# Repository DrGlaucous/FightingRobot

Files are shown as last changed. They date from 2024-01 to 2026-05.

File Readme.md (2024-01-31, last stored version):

# Remote Vehicle repository

This is where I put everything relating to designing a small, "antweight" combat robot.

## Firmware
Currently, the firmware is programmed in platform.io around the STM32 architecture.
The vehicle communicates to the controller using the RFM69HW radio module, which is both inexpensive and has excellent transmission range.

The "Transmitter" module decodes [PPM signals](http://flyingeinstein.com/index.php/articles/58-ppm-explained) from the controller and sends their digital values over the radio to the vehicle. There *are* recievers that output PPM directly without the need for the RFM middleman, but those are expensive and radio-specific. The extra range those modules would provide would be moot in the context of miniature combat robots. The analog transmitters additionally do not provide the customization abillity the digital transmiter has.

The work with RFM69 radios builds upon my previous project where I made an [inexpensive iClicker alternative using just the radio and an STM32](https://github.com/DrGlaucous/LittleBuddy). That repository better outlines how the STM32 should be connected to the RFM69 module.

---

<details>
  <summary style="font-size:100%;"><i><b>Notes for me</b></i></summary>

### Future Goals
Either use an ESP32 on the vehicle-side, or add bidirectional DShot to the STM32, so the vehicle's motor will provide telemetry.

### Mobility
With the transmitter, more flexible motion can be implemented.

Current suggestion: 3 wheeled omniwheel wheelbase

### Weapons

Rotating offset platic blade on one side, must not be below or above the robot's dirve train so it can drive upside down or rightside up.

Or long, plastic wedge attached to a servo motor for flipping other robots.

</details>

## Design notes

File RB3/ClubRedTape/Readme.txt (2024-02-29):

Things required by the club this robot is entered into in order to get it certified and usable.

these CAD files must also be on arris
part naming conventsions:

[4-letter-code]-[A/P - assembly/part]-[2 digit asm ID][2 digit part ID]Name
example:
OMNI-P-0203SideStrut

ASM Ids:
00 - top
1 - asm sketch
2 - chassis
3 - drivebase
4 - weapon1
5 - weapon2
6 - ground game (wedges/forks)

(also, it all has to be in solidworks, for some reason...)

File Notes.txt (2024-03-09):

hardware SPI on an ESP32:
default:

VSPI:
MOSI 23
MISO 19
SCLK 18
CS 5

HSPI
MOSI 13
MISO 12
SCLK 14
CS 15

in arduino IDE, these are defined as their respective names
(note: these pins can be changed)

to change SPI pins manually in a library that doesn't support custom initialization, use:
SPI.begin(SCK, MISO, MOSI, SS);

for multiple SPI busses, initialize
vspi = new SPIClass(VSPI);
hspi = new SPIClass(HSPI);

see more:
https://randomnerdtutorials.com/esp32-spi-communication-arduino/

on top and bottom walls, other robots use 1.5-2mm thick shells

(we could probably do this for the internal structure as well)

for edge walls, 3-5mm will suffice (put curves so the robot cannot sit on them)

Futaba 12 channel troubles:

reset line is

long time LOW->long time HIGH

each channel has a LOW time that matches a HIGH time

A channel may unexpectedly cut out before transmission is complete, completing a "cycle" prematurely.
it will wait at least one complete cycle before finishing the half-done channel.

in order to ensure that we get good signals every time, we need to detect the bad channel pauses.
The easiest way to (possibly) do this is to only update all the channel values if we get all of them in one go.

if we detect a reset rollover, we then move the waiting signals over to the visible surface ONLY if we got all of them. Partials will not count.

have roughly 7 Oz on frame

1.295 allocated for screws, worst case

5.705 left for frame
(some screws can be ommitted/glue used instead)

16 Oz max

1.0005 - PCB + componets
3.327 - wheels + n20s * 3
1.01 - 2205
0.30 - ESC
0.976 - servos
2 - battery
1.295 - screws

-9.88 for all of this

2.196 - side walls

6 Ounces/170 grams to work with

Blade: 9g
Internal frame (as-is) + arm: 84

(thin top shell, both sides: 60g)

12.08 total rn + side walls

oz
3.73 - walls+roof
0.81 - mot1
2.6320 - mot2
2.238 - wheels3
2.74 - chassis + electrics
2.00 - battery
14.292 - total

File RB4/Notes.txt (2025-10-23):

BOM items:

x2 4mm motors

optional amazon things:
openWRT router
large bullet connectors
4mm bearings

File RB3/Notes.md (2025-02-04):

### BOM

- 1 lolin32 lite
- 1 littlebee ESC
- 1 2205 brushless motor
- 1 motor driver
- x2 n30 motors + encoders
- 3d prints

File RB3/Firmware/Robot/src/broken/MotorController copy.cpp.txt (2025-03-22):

#include <Arduino.h>
#include <math.h>
#include "configuration.h"
#include "PidController.h"
#include "MotorController.h"

static void isr_0();
static Apple* this_0;

static void isr_1();
static Apple* this_1;

void isr_0() {
    this_0->isr_handler();
}
void isr_1() {
    this_1->isr_handler();
}

void Apple::isr_handler() {

    bool CLKstate = digitalRead(enca_pin);
    bool DTstate = digitalRead(encb_pin);

    switch (encoder_state) {
        case 0:                         // Idle state, encoder not turning
            if (!CLKstate){             // Turn clockwise and CLK goes low first
                encoder_state = 1;
            } else if (!DTstate) {      // Turn anticlockwise and DT goes low first
                encoder_state = 4;
            }
            break;
        // Clockwise rotation
        case 1:                     
            if (!DTstate) {             // Continue clockwise and DT will go low after CLK
                encoder_state = 2;
            } 
            break;
        case 2:
            if (CLKstate) {             // Turn further and CLK will go high first
                encoder_state = 3;
            }
            break;
        case 3:
            if (CLKstate && DTstate) {  // Both CLK and DT now high as the encoder completes one step clockwise
                encoder_state = 0;
                ++encoder_value;
            }
            break;
        // Anticlockwise rotation
        case 4:                         // As for clockwise but with CLK and DT reversed
            if (!CLKstate) {
                encoder_state = 5;
            }
            break;
        case 5:
            if (DTstate) {
                encoder_state = 6;
            }
            break;
        case 6:
            if (CLKstate && DTstate) {
                encoder_state = 0;
                --encoder_value;
            }
            break; 
    }

}

/*
MotorController::MotorController(
    int enca_pin,
    int encb_pin,
    int motor_a_pin,
    int motor_b_pin,
    IsrSlotNumber slot_num
    ) {
    
    this->enca_pin = enca_pin;
    this->encb_pin = encb_pin;
    this->motor_a_pin = motor_a_pin;
    this->motor_b_pin = motor_b_pin;

    this->has_began = false;
    
    this->slot_num = slot_num;

    motor_pid = PIDControllerF_construct(
        ANALOG_MIN,
        ANALOG_MAX,
        -ANALOG_MAX,
        0.2, //p
        0.2, //i
        0.2 //d
    );

    //set proper ISR
    switch(slot_num) {
        case IsrSlotZero: {
            this_0 = this;
            attachInterrupt(enca_pin, isr_0, CHANGE);
            attachInterrupt(encb_pin, isr_0, CHANGE);
            break;
        }
        case IsrSlotOne: {
            this_1 = this;
            attachInterrupt(enca_pin, isr_0, CHANGE);
            attachInterrupt(encb_pin, isr_0, CHANGE);
            break;
        }
    }

}
*/

Apple::Apple() {

}

Apple::~Apple() {
    PIDControllerF_destruct(motor_pid);

    detachInterrupt(enca_pin);
    detachInterrupt(encb_pin);

    // switch(slot_num) {
    //     case IsrSlotZero: {
    //         this_0 = this;
    //         detachInterrupt(enca_pin);
    //         detachInterrupt(encb_pin);
    //         break;
    //     }
    //     case IsrSlotOne: {
    //         this_1 = this;
    //         attachInterrupt(enca_pin, isr_0, CHANGE);
    //         attachInterrupt(encb_pin, isr_0, CHANGE);
    //         break;
    //     }
    // }
}

void Apple::begin() {
    //set up IO
    pinMode(motor_a_pin, OUTPUT);
    pinMode(motor_b_pin, OUTPUT);
    pinMode(enca_pin, INPUT);
    pinMode(encb_pin, INPUT);

    analogWrite(motor_a_pin, ANALOG_MIN);
    analogWrite(motor_b_pin, ANALOG_MIN);

    has_began = true;

}

float Apple::tick(int target_speed, bool is_disabled, bool direct_speed_map) {

    //inputs
    //int target_speed = 0; //raw controller speed (from NORMAL_MIN to NORMAL_MAX)
    //bool is_disabled = false; //true when the main robot disables the motor controller

    //true when the input speed should be mapped directly to the motors
    //can be used if the PID breaks or something
    //bool direct_speed_map = false;

    //must have initialized and be enabled
    if(!has_began || is_disabled) {
        return 0.0;
    }

    //note: this may not be used, depending on stability (with my nerf blaster, using a non-constant for this resulted in trouble)
    int milliss = millis();

    //do not run if no time has elapsed
    // if(milliss == last_millist) {
    //     return 0.0;
    // }

    //turn raw controller input into a target RPM speed for the motor
    //note: 200 ticks per rotation

    //get current RPM (may be less than one per tick)
    float curr_rpm = 0.0;
    {
        int delta_ticks = motor_tick_ct - last_motor_tick_ct;
        float tick_fraction = 0.0;

        if(delta_ticks) {
            time_since_motor_tick = 0;
            tick_fraction = delta_ticks;
        } else {
            time_since_motor_tick++;
            tick_fraction = 1.0 / ((float)time_since_motor_tick);
        }

        //tick_fraction is the number of ticks we have since the last time checked

        float minutes_elapsed = ((float)(milliss - 0) * 0.001 * 0.016666);
        float rpm = tick_fraction / minutes_elapsed;

        curr_rpm = tick_fraction;
        last_motor_tick_ct = motor_tick_ct;
    }

    if(direct_speed_map) {
        motor_output = map(target_speed, NORMAL_MIN, NORMAL_MAX, -ANALOG_MAX, ANALOG_MAX);
    } else {

        int mapped_target_speed = rpm_to_ticks(map(target_speed, NORMAL_MIN, NORMAL_MAX, -100, 100));
        PIDControllerF_tick(motor_pid, FLOAT_TO_FIXED32(curr_rpm), INT_TO_FIXED32(mapped_target_speed), 200); //feeding constant time step of 200 into the PID
    }

    //last_millist = milliss;

    return curr_rpm;

}

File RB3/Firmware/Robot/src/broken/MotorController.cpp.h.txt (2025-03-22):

#pragma once

#define ANALOG_MAX 255
#define ANALOG_MIN 0

typedef enum IsrSlotNumber {
    IsrSlotZero,
    IsrSlotOne
}IsrSlotNumber;

class MotorController{

    public:

    MotorController(
        int enca_pin,
        int encb_pin,
        int motor_a_pin,
        int motor_b_pin,
        IsrSlotNumber sl
    );

    ~MotorController();

    void begin();

    float tick(int target_speed, bool is_disabled, bool direct_speed_map);

    void isr_handler();

    private:

    int enca_pin = -1;
    int encb_pin = -1;
    int motor_a_pin = -1;
    int motor_b_pin = -1;

    int motor_output = 0; //value to be written to the motor (result of the PID or direct mapping)
    bool has_began = false;

    int last_millis = 0;
    int motor_tick_ct = 0; //holds raw absolute position of the motor
    int last_motor_tick_ct = 0; //for delta ticks
    int time_since_motor_tick = 0; //holds the number of cycles since the last encoder change interrupt

    // uint8_t encoder_state = 0;

    // PIDControllerF* motor_pid = NULL;
    // IsrSlotNumber slot_num = IsrSlotOne; //keep track of this for removing ISR on destruct
    // int32_t encoder_value = 0;

    // // //isrs (one for each instance of the class we can run)
    // // static void isr_0();
    // // static MotorController* this_0;

    // // static void isr_1();
    // // static MotorController* this_1;

};

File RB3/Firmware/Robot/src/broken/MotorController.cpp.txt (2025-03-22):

#include "Apple.h"

int rpm_to_ticks(int rpm) {
    return rpm * 200;
}

void MotorController::isr_handler() {

}

MotorController::MotorController(
    int enca_pin,
    int encb_pin,
    int motor_a_pin,
    int motor_b_pin,
    IsrSlotNumber sl
    ) {

}

MotorController::~MotorController() {

}

void MotorController::begin() {

}

float MotorController::tick(int target_speed, bool is_disabled, bool direct_speed_map) {
    return 0.0;
}

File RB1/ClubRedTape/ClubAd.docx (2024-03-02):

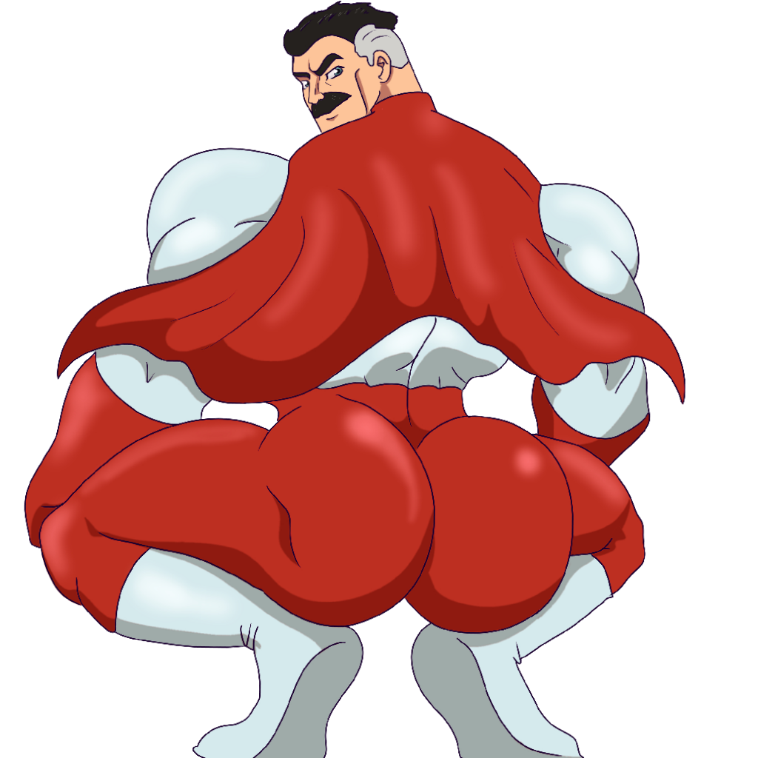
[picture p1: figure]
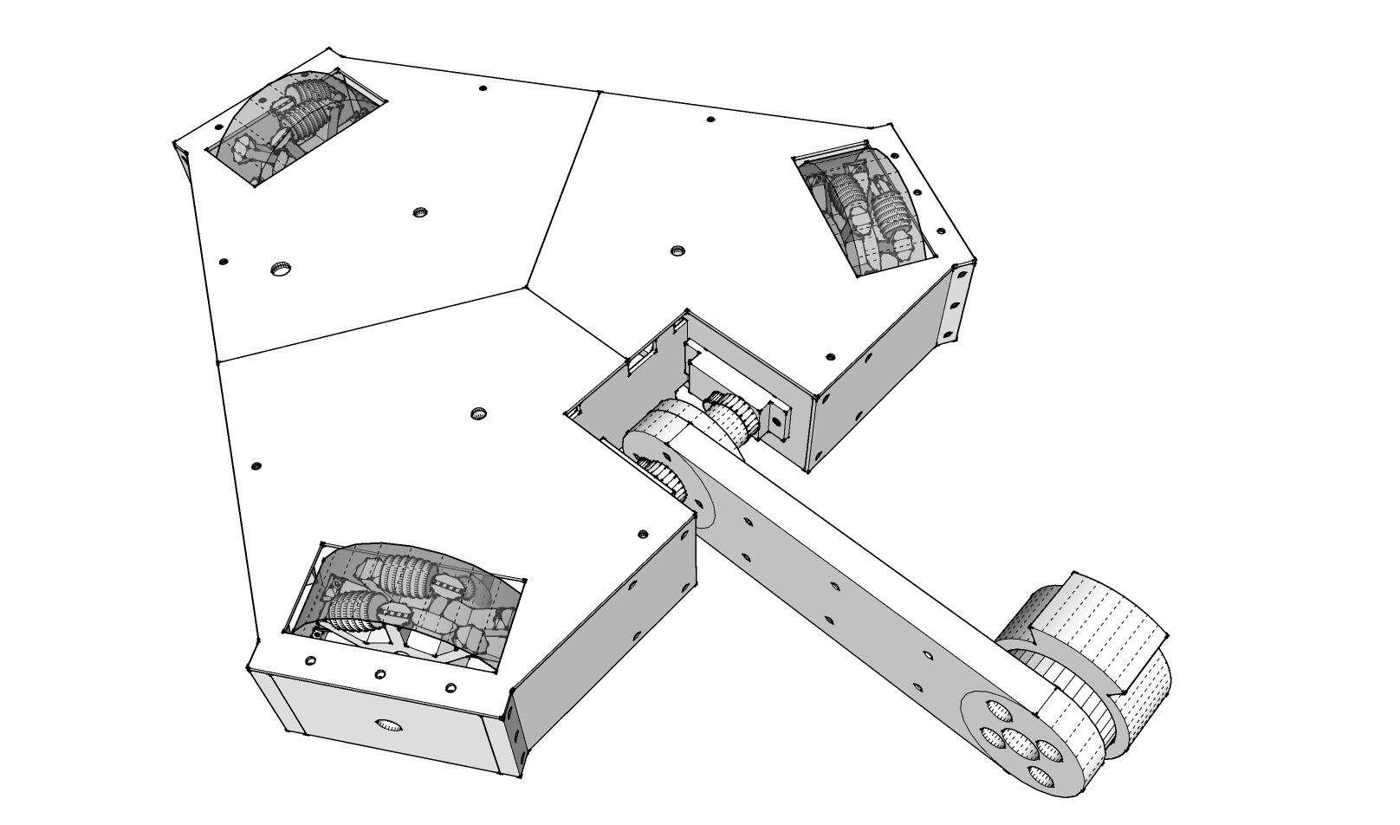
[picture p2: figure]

See this robot dump its truck on others like it on 3/23/2024 at 10:00 AM in Aspire Building A. The event is free to watch!

At the 2024 Railside Robotics

Battlebot Brawl!

Root for Omni-Man!

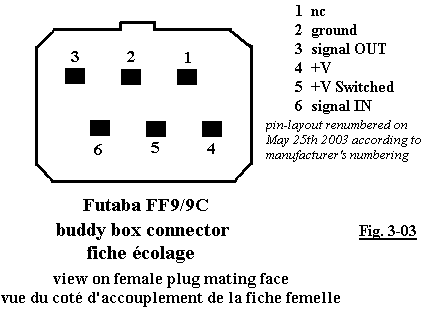
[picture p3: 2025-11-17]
Resource/Futaba trainer port pinout.gif

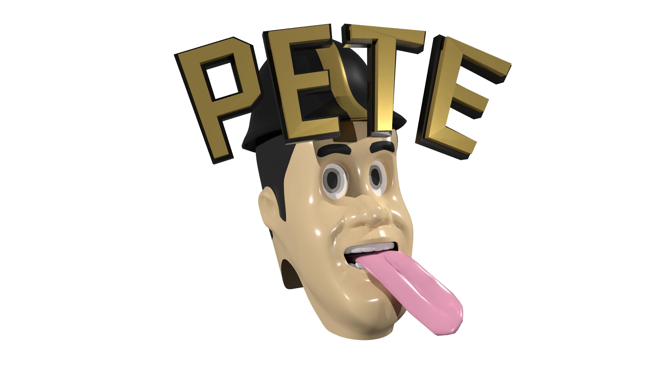
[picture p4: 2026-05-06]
RB4/Media/Pete.png

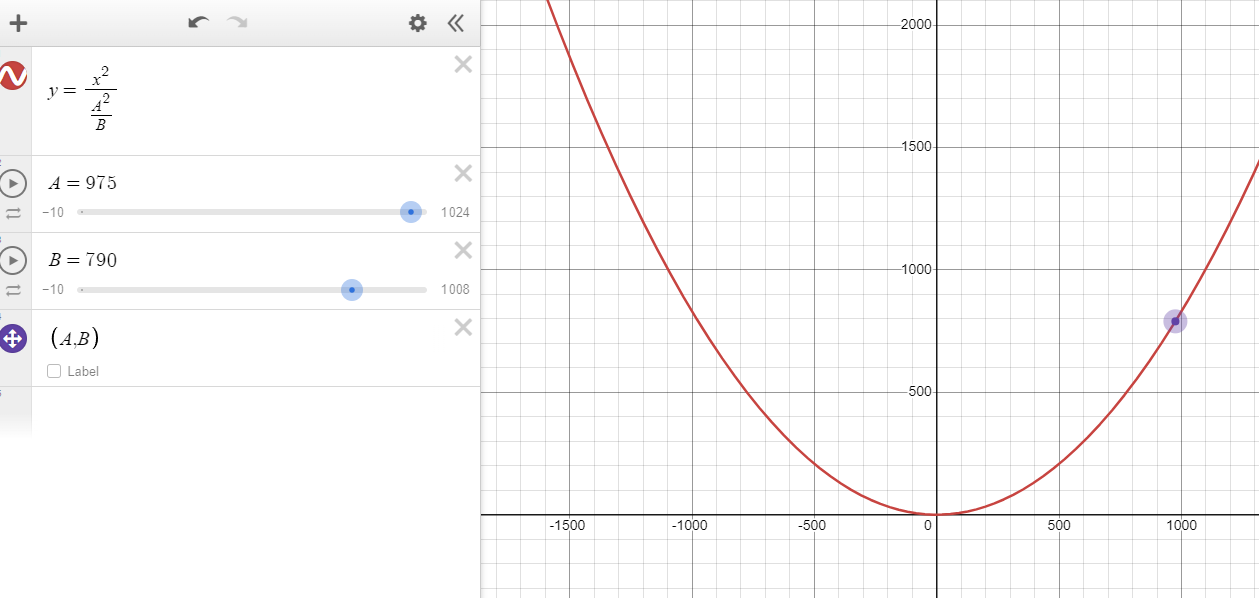
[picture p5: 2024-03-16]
RB1/Resource/ExponentialMapping.PNG

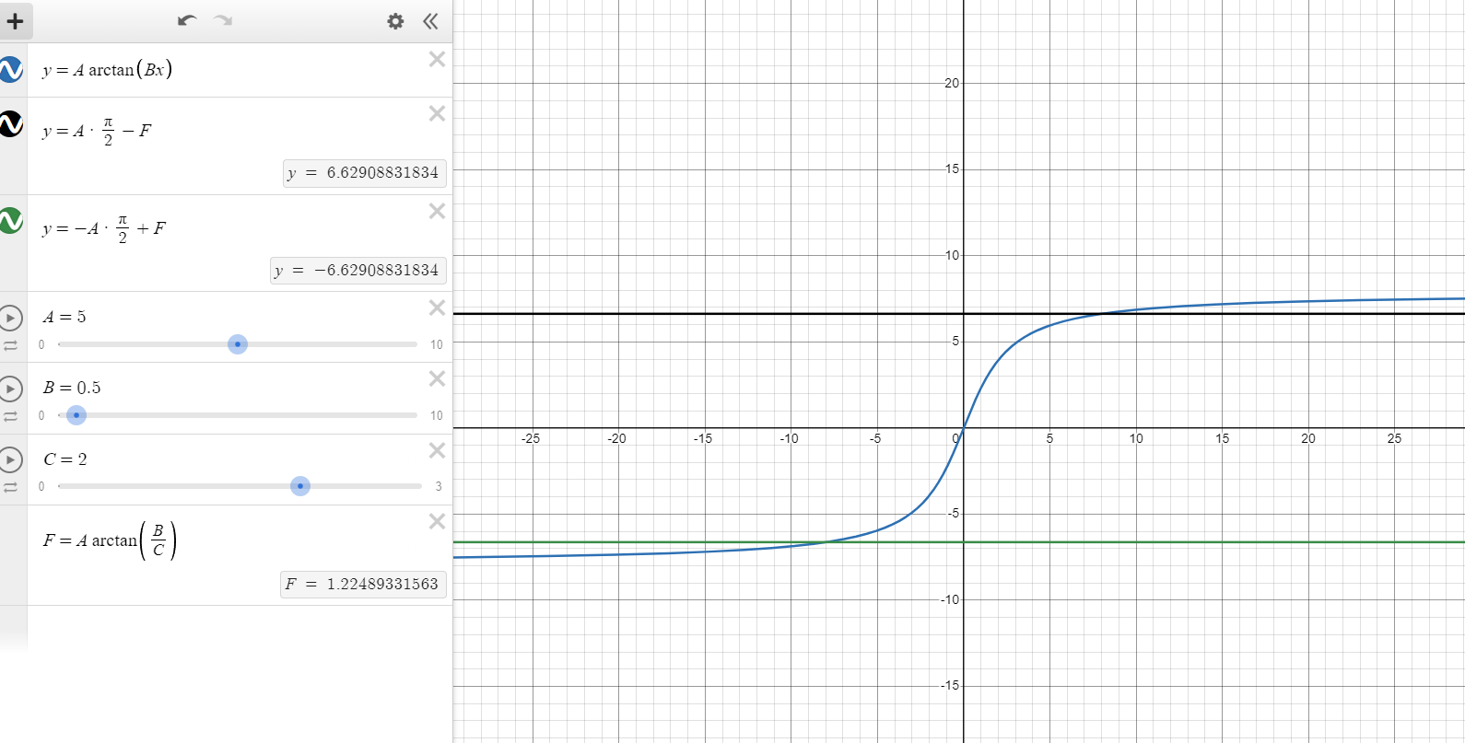
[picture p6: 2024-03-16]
RB1/Resource/MotorSpeedRampFunction.PNG

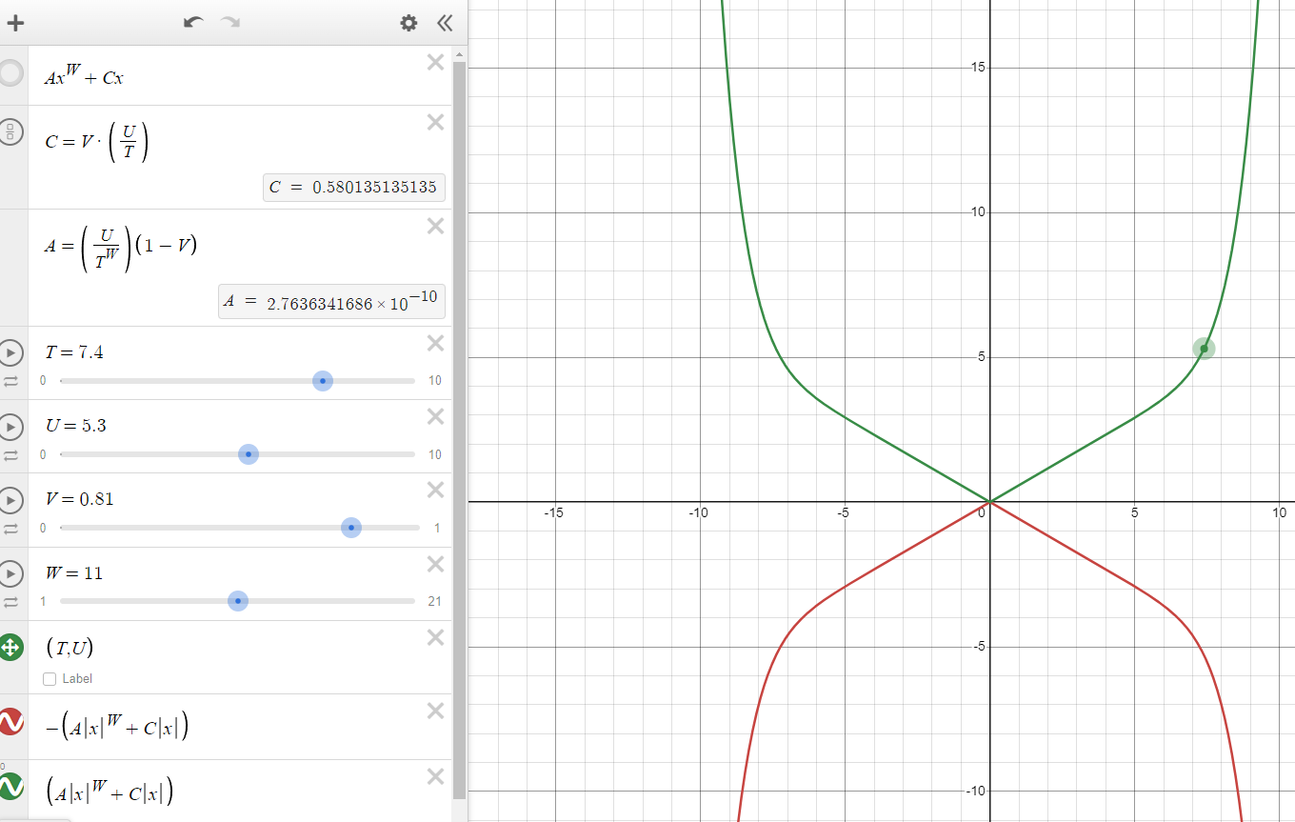
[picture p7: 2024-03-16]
RB1/Resource/RotattionRampEquation.PNG

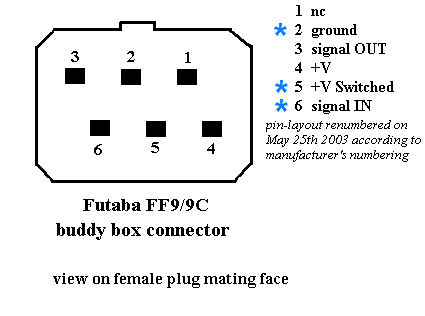
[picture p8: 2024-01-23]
RB1/Resource/futabaplug.jpg

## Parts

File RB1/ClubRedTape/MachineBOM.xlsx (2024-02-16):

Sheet: BOM
DO NOT ENTER VALUES FOR COLUMNS HIGHLIGHTED GREEN
Overall Bot Value: |  | $84.35 | External Component $ Spent: | $202.96 | Railside $ Spent: | $30.74 | Total $ Spent: | $233.70
Category | Qty | Item | Specs | Item Description | Vendor/Source | Link | Units per Package | Units per Bot | Provided by Railside? | Item Cost | What is the part for? | Unit Cost | Unit/Bot Cost | Total Cost
 | 1 | Fingertech Mini Power Switch | N.A. | Screw switch used to turn robot on / off | Itgresa | https://itgresa.com/product/mini-power-switch/ | 1 | 1 | yes | $7.99 | Required Safety | $7.99 | $7.99 | $7.99
 | 1 | Tattu 450 mAh 2S LiPo with XT30 | 75C 450mAh | Battery to power the robot | Amazon | https://www.amazon.com/TATTU-450mAh-Battery-Pack-H-Frame/dp/B07DTYN9QF?s=electronics | 1 | 1 | yes | $12.95 | Power | $12.95 | $12.95 | $12.95
 | 1 | N20 gearmotor | 12 Volt, 1000 RPM | For Robot Drive Base | AliExpress | https://www.aliexpress.com/item/2251832836005412.html | 1 | 3 | no | $1.68 | Mobility | $1.68 | $5.04 | $1.68
 | 1 | N20 gearmotor (alt. source) | 12 Volt, 800 RPM | Alt. Club provided Drive Base motors | itgresa | https://itgresa.com/product/turnabot-n20-motors-1400rpm/ | 1 | 3 | yes | $9.80 | Mobility (backup) | $9.80 | $29.40 | $9.80
 | 1 | RFM69HW Radio Tranciever | 915Mhz, 1.4kbps | For remote interfacing | AliExpress | https://www.aliexpress.com/item/3256803259645975.html | 1 | 2 | no | $1.66 | Remote Control | $1.66 | $3.32 | $1.66
Electronics | 1 | LittleBee ESC | BLHELI_S, 30A | For driving the weapon | Amazon | https://www.amazon.com/LITTLEBEE-Mulitshot-Oneshot42-OneShot125-Multicopter/dp/B09P44FKKQ | 4 | 1 | no | $30.00 | Weapon Driver | $7.50 | $7.50 | $30.00
 | 1 | 2205 Emax Motor | 2300KV, 2205 | Used as the weapon | Amazon | https://www.amazon.com/AKK-RS2205-Brushless-2300KV-Quadcopter/dp/B07BQRGT7Q | 4 | 1 | no | $31.99 | Weapon | $8.00 | $8.00 | $31.99
 | 1 | Fuse | 15A max | Overcurrent safety | Unknown |  | 2 | 2 | yes | $0.00 | Required Safety | $0.00 | $0.00 | $0.00
 | 1 | DRV8833 DC motor driver | handles 2 motors | For Robot Drive Base | AliExpress | https://www.aliexpress.com/item/3256806258295019.html | 10 | 2 | no | $4.64 | Mobility | $0.46 | $0.93 | $4.64
 | 1 | XL60009 Boost module | 4A in max, 12 volts out | Motor power supply | Amazon | https://www.amazon.com/AITRIP-Voltage-Adjustable-Step-up-Converter/dp/B08FM414QN | 10 | 1 | no | $14.00 | Power Regulation | $1.40 | $1.40 | $14.00
 | 1 | Mini360 Buck module | 3.3 volt out | Logic power supply | AliExpress | https://www.aliexpress.us/item/3256806205076602.html | 20 | 1 | no | $2.00 | Power Regulation | $0.10 | $0.10 | $2.00
 | 1 | Lolin32 LITE | 32 bit microcontroller | Bot controller | AliExpress | https://www.aliexpress.com/item/3256801612417572.html | 1 | 1 | no | $2.12 | Bot Control | $2.12 | $2.12 | $2.12
 | 1 | STM32 Bluepill | 32 bit microcontroller | Transmitter controller | AliExpress | https://www.aliexpress.us/item/3256806245533637.html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 | 10 | 1 | no | $14.00 | Remote Control | $1.40 | $1.40 | $14.00
 | 1 | MG90S Servo | All-metal MG90S | micro servo | AliExpress | https://www.aliexpress.com/item/3256805876746809.html | 10 | 2 | no | $16.37 | Weapon | $1.64 | $3.27 | $16.37
 |  | Things like power transmission members (belts, pulleys), bot materials (3D printer filament), wheels, bushings/bearings, etc go here |  |  |  |  |  |  |  | $0.00 |  | $0.00 | $0.00 | $0.00
 | 1 | ABS (Home-Extruded) | PA757 | Natural uncolored ABS | Filastruder |  | 50 | 0.5 | no | $80.00 | Frame | $1.60 | $0.80 | $80.00
Structure / Materials | 1 |  |  |  |  |  |  |  |  | $0.00 |  | $0.00 | $0.00 | $0.00
 | 1 |  |  |  |  |  |  |  |  | $0.00 |  | $0.00 | $0.00 | $0.00
 | 1 |  |  |  |  |  |  |  |  | $0.00 |  | $0.00 | $0.00 | $0.00
 |  | Screws, nuts, shoulder bolts go here |  |  |  |  |  |  |  | $0.00 |  | $0.00 | $0.00 | $0.00
 | 1 | 6-32x1-1/2 Phillips screw | 6-32x1-1/2 | Machine screw | Menards | In-store | 100 | 3 | no | $2.25 | Fasteners | $0.02 | $0.07 | $2.25
Hardware (Fasteners) | 1 | 6-32 Hex Nut | 6-32 size | Machine nut | Menards | In-Store | 100 | 3 | no | $2.25 | Fasteners | $0.02 | $0.07 | $2.25
 | 1 | Plastic Screw | #4 | self-tapping screw | Amazon | https://www.amazon.com/Thread-Rolling-Plastic-Finish-Degree/dp/B00GDYNQBM | 100 | 50 | yes | $0.00 | Fasteners | $0.00 | $0.00 | $0.00
 |  |  |  |  |  |  |  |  |  | $0.00 |  | $0.00 | $0.00 | $0.00
 |  | Anything that doesnt fit into the above category |  |  |  |  |  |  |  | $0.00 |  | $0.00 | $0.00 | $0.00
 |  |  |  |  |  |  |  |  |  | $0.00 |  | $0.00 | $0.00 | $0.00
Misc. |  |  |  |  |  |  |  |  |  | $0.00 |  | $0.00 | $0.00 | $0.00
 |  |  |  |  |  |  |  |  |  | $0.00 |  | $0.00 | $0.00 | $0.00
 |  |  |  |  |  |  |  |  |  | $0.00 |  | $0.00 | $0.00 | $0.00
 |  |  |  |  |  |  |  |  |  | $0.00 |  | $0.00 | $0.00 | $0.00
 |  |  |  |  |  |  |  |  |  | $0.00 |  | $0.00 | $0.00 | $0.00
 |  |  |  |  |  |  |  |  |  | $0.00 |  | $0.00 | $0.00 | $0.00
 |  |  |  |  |  |  |  |  |  | $0.00 |  | $0.00 | $0.00 | $0.00
 |  |  |  |  |  |  |  |  |  | $0.00 |  | $0.00 | $0.00 | $0.00
 |  |  |  |  |  |  |  |  |  | $0.00 |  | $0.00 | $0.00 | $0.00
 |  |  |  |  |  |  |  |  |  | $0.00 |  | $0.00 | $0.00 | $0.00
 |  |  |  |  |  |  |  |  |  | $0.00 |  | $0.00 | $0.00 | $0.00
 |  |  |  |  |  |  |  |  |  | $0.00 |  | $0.00 | $0.00 | $0.00
 |  |  |  |  |  |  |  |  |  | $0.00 |  | $0.00 | $0.00 | $0.00
 |  |  |  |  |  |  |  |  |  | $0.00 |  | $0.00 | $0.00 | $0.00
 |  |  |  |  |  |  |  |  |  | $0.00 |  | $0.00 | $0.00 | $0.00
 |  |  |  |  |  |  |  |  |  | $0.00 |  | $0.00 | $0.00 | $0.00

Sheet: Equations
Input yellow values | Green values will automatically be calculated
Battery
Cells | Voltage Level | Voltage Multiplier | Voltage (V)
2 | max | 4.2 | 8.4
Weapon Motor
Kv (rpm/V) | Throttle % | RPM | Kv (rad/s/V)
0 | 100 | 0 | 0
Weapon
Moment of Inertia (g*mm^2) | Diameter (in) | Weapon Reduction
0 | 0 | 1
MOI (kg*m^2) | RPM | (rev/s) | Angular Velocity (rad/s)
0 | 0 | 0 | 0
Kinetic Energy (Joules) | Tip Speed (in/s) | Tip Speed (mph)
0 | 0 | 0
Bite
Impactor Count | Max Impactor Angle (fraction) | Seconds per Hit (s) | Max Bite (in)
0 | #DIV/0! | #DIV/0! | #DIV/0!
Drive Motor
RPM | Throttle % | RPM
0 | 100 | 0
Drive
Wheel Diameter (in) | Speed (in/min) | Speed (mph) | Speed (in/s)
0 | 0 | 0 | 0

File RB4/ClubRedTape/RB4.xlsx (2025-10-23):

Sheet: BOM
DO NOT ENTER VALUES FOR COLUMNS HIGHLIGHTED GREEN
Overall Bot Value: |  | $59.47 | External Component $ Spent: | $25.90 | Railside $ Spent | $4.99 | Total $ Spent: | $30.89
Category | Qty | Item | Ordering Specs | Vendor/Source | Link | Subsystem | Units per Package | Units per Bot | Provided by Railside? | Item Cost | What is the part for? | Unit Cost | Unit/Bot Cost | Total Cost
 | 1 | PCB power switch |  | JustCuz | https://justcuzrobotics.com/products/switch | Electronics | 1 | 1 | yes | $4.99 | Robot power | $4.99 | $4.99 | $4.99
 | 2 | 1200 mAh 2S LiPo with XT30 |  | Amazon | https://www.amazon.com/URGENEX-Battery-1200mAh-Rechargeable-Compatible/dp/B0DZNYQWD4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 (https://www.amazon.com/TATTU-450mAh-Battery-Pack-H-Frame/dp/B07DTYN9QF?s=electronics) | Electronics | 2 | 1 | no | $12.95 | Robot power | $6.47 | $6.47 | $25.90
 |  | Drive motors, mk.2 brushed, 4mm shaft |  | Repeat Robotics | https://repeat-robotics.com/buy/brushed/ | Drivetrain | 1 | 2 | no | $20.00 | robot drive | $20.00 | $40.00 | $0.00
 |  | ESP32 - C3 |  | aliExpress | N.A | Electronics | 1 | 1 | no | $2.00 | robot control | $2.00 | $2.00 | $0.00
Electronics |  | DRV8833 |  | aliExpress | N.A | Electronics | 1 | 1 | no | $1.00 | motor control | $1.00 | $1.00 | $0.00
 |  | MG996R servo |  | aliExpress | N.A | Weapon | 1 | 1 | no | $5.00 | weapon drive | $5.00 | $5.00 | $0.00
 |  | RFM69HW Radio |  | aliExpress | N.A | Electronics |  |  |  | $0.00 | communication | $0.00 | $0.00 | $0.00
 |  | Fuse |  | N.A. |  |  |  |  |  | $0.00 | Fuse not needed | $0.00 | $0.00 | $0.00
 |  |  |  |  |  |  |  |  |  | $0.00 |  | $0.00 | $0.00 | $0.00
 |  | TPU Filament |  |  |  | Chassis |  |  |  | $0.00 | Bot frame | $0.00 | $0.00 | $0.00
Structure / Materials |  |  |  |  |  |  |  |  |  | $0.00 |  | $0.00 | $0.00 | $0.00
 |  |  |  |  |  |  |  |  |  | $0.00 |  | $0.00 | $0.00 | $0.00
 |  | N.A.
Power Transmission |  |  |  |  |  |  |  |  |  | $0.00 |  | $0.00 | $0.00 | $0.00
 |  |  |  |  |  |  |  |  |  | $0.00 |  | $0.00 | $0.00 | $0.00
 |  | Screws, nuts, shoulder bolts go here |  |  |  |  |  |  |  | $0.00 |  | $0.00 | $0.00 | $0.00
 |  | Plastic screws, club supplied (1/2 inch) |  | X |  | Chassis | X | 15 | yes | $0.00 | Bot fasteners | $0.00 | $0.00 | $0.00
Hardware (Fasteners) |  | Plastic screws, club supplied (3/4 inch) |  | X |  | Chassis | X | 10 | yes | $0.00 | Bot fasteners | $0.00 | $0.00 | $0.00
 |  |  |  |  |  |  |  |  |  | $0.00 |  | $0.00 | $0.00 | $0.00
 |  |  |  |  |  |  |  |  |  | $0.00 |  | $0.00 | $0.00 | $0.00
 |  | Anything that doesnt fit into the above category |  |  |  |  |  |  |  | $0.00 |  | $0.00 | $0.00 | $0.00
 |  |  |  |  |  |  |  |  |  | $0.00 |  | $0.00 | $0.00 | $0.00
Misc. |  |  |  |  |  |  |  |  |  | $0.00 |  | $0.00 | $0.00 | $0.00
 |  |  |  |  |  |  |  |  |  | $0.00 |  | $0.00 | $0.00 | $0.00
 |  |  |  |  |  |  |  |  |  | $0.00 |  | $0.00 | $0.00 | $0.00
 |  |  |  |  |  |  |  |  |  | $0.00 |  | $0.00 | $0.00 | $0.00
 |  |  |  |  |  |  |  |  |  | $0.00 |  | $0.00 | $0.00 | $0.00
 |  |  |  |  |  |  |  |  |  | $0.00 |  | $0.00 | $0.00 | $0.00
 |  |  |  |  |  |  |  |  |  | $0.00 |  | $0.00 | $0.00 | $0.00
 |  |  |  |  |  |  |  |  |  | $0.00 |  | $0.00 | $0.00 | $0.00
 |  |  |  |  |  |  |  |  |  | $0.00 |  | $0.00 | $0.00 | $0.00
 |  |  |  |  |  |  |  |  |  | $0.00 |  | $0.00 | $0.00 | $0.00
 |  |  |  |  |  |  |  |  |  | $0.00 |  | $0.00 | $0.00 | $0.00
 |  |  |  |  |  |  |  |  |  | $0.00 |  | $0.00 | $0.00 | $0.00
 |  |  |  |  |  |  |  |  |  | $0.00 |  | $0.00 | $0.00 | $0.00
 |  |  |  |  |  |  |  |  |  | $0.00 |  | $0.00 | $0.00 | $0.00
 |  |  |  |  |  |  |  |  |  | $0.00 |  | $0.00 | $0.00 | $0.00
 |  |  |  |  |  |  |  |  |  | $0.00 |  | $0.00 | $0.00 | $0.00

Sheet: Physics Equations
Input yellow values | Green values will automatically be calculated
Battery
Cells | Voltage Level | Voltage Multiplier | Voltage (V)
3 | nominal | 3.7 | 11.1
Weapon Motor
Kv (rpm/V) | Throttle % | RPM | Kv (rad/s/V)
1800 | 100 | 19980 | 188.4955592
Weapon
Moment of Inertia (g*mm^2) | Diameter (in) | Weapon Reduction
244900 | 4 | 1
MOI (kg*m^2) | RPM | (rev/s) | Angular Velocity (rad/s)
0.0002449 | 19980 | 333 | 2092.300707
Kinetic Energy (Joules) | Tip Speed (in/s) | Tip Speed (mph)
536.0520895 | 4184.601415 | 237.761444
Bite
Impactor Count | Max Impactor Angle (fraction) | Seconds per Hit (s) | Max Bite (in)
1 | 1 | 0.003003003003 | 0.2515789913
Drive Motor
RPM | Throttle % | RPM
800 | 100 | 800
Drive
Wheel Diameter (in) | Speed (in/min) | Speed (mph) | Speed (in/s)
2 | 5026.548246 | 4.759988869 | 83.7758041

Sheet: Wire Sizing Chart
 |  |  |  |  |  |  |  |  |  | Factor of Safety for Maximum Voltage Drop due to Wire Resistancce
AWG | Diameter (mm) | Area (mm^2) | Resistance Copper (ohm/1000m) | Resistance 1 inch (ohm) | System Voltage: | 12.6 | V |  |  | Wire Run Length (in)
 |  |  |  |  | Max V Drop: | 0.100 | V | Ohm/In | AWG | 1 | 2 | 3 | 4 | 6 | 8 | 10 | 12 | 18 | 24 | 30 | 60
 |  |  |  |  | Set Current: | 15 | A | 0.0033782 | 26 | 2.0 | 1.0 | 0.7 | 0.5 | 0.3 | 0.2 | 0.2 | 0.2 | 0.1 | 0.1 | 0.1 | 0.03289062551
26 | 0.41 | 0.13 | 133 | 0.0033782 | Max Power Loss: | 1.5 | W | 0.0022352 | 24 | 3.0 | 1.5 | 1.0 | 0.7 | 0.5 | 0.4 | 0.3 | 0.2 | 0.2 | 0.1 | 0.1 | 0.04970969538
24 | 0.51 | 0.2 | 88 | 0.0022352 |  |  |  | 0.0013208 | 22 | 5.0 | 2.5 | 1.7 | 1.3 | 0.8 | 0.6 | 0.5 | 0.4 | 0.3 | 0.2 | 0.2 | 0.1
22 | 0.64 | 0.33 | 52 | 0.0013208 |  |  |  | 0.0008636 | 20 | 7.7 | 3.9 | 2.6 | 1.9 | 1.3 | 1.0 | 0.8 | 0.6 | 0.4 | 0.3 | 0.3 | 0.1
20 | 0.81 | 0.5 | 34 | 0.0008636 |  |  |  | 0.0005334 | 18 | 12.5 | 6.2 | 4.2 | 3.1 | 2.1 | 1.6 | 1.2 | 1.0 | 0.7 | 0.5 | 0.4 | 0.2
18 | 1 | 0.82 | 21 | 0.0005334 |  |  |  | 0.0003302 | 16 | 20.2 | 10.1 | 6.7 | 5.0 | 3.4 | 2.5 | 2.0 | 1.7 | 1.1 | 0.8 | 0.7 | 0.3
16 | 1.3 | 1.3 | 13 | 0.0003302 |  |  |  | 0.00020828 | 14 | 32.0 | 16.0 | 10.7 | 8.0 | 5.3 | 4.0 | 3.2 | 2.7 | 1.8 | 1.3 | 1.1 | 0.5
14 | 1.6 | 2.1 | 8.2 | 0.00020828 |  |  |  | 0.00013208 | 12 | 50.5 | 25.2 | 16.8 | 12.6 | 8.4 | 6.3 | 5.0 | 4.2 | 2.8 | 2.1 | 1.7 | 0.8
12 | 2.1 | 3.3 | 5.2 | 0.00013208 |  |  |  | 8.382e-05 | 10 | 79.5 | 39.8 | 26.5 | 19.9 | 13.3 | 9.9 | 8.0 | 6.6 | 4.4 | 3.3 | 2.7 | 1.3
10 | 2.6 | 5.3 | 3.3 | 8.382e-05 |  |  |  | 5.334e-05 | 8 | 125.0 | 62.5 | 41.7 | 31.2 | 20.8 | 15.6 | 12.5 | 10.4 | 6.9 | 5.2 | 4.2 | 2.1
8 | 3.3 | 8.3 | 2.1 | 5.334e-05 |  |  |  | 3.302e-05 | 6 | 201.9 | 100.9 | 67.3 | 50.5 | 33.6 | 25.2 | 20.2 | 16.8 | 11.2 | 8.4 | 6.7 | 3.4
6 | 4.1 | 13.3 | 1.3 | 3.302e-05 |  |  |  |  |  | Voltage Drop due to Wire Resistance
 |  |  |  |  |  |  |  |  |  | Wire Run Length (in)
 |  |  |  |  |  |  |  | Ohm/In | AWG | 1 | 2 | 3 | 4 | 6 | 8 | 10 | 12 | 18 | 24 | 30 | 60
 |  |  |  |  |  |  |  | 0.0033782 | 26 | 0.05 | 0.10 | 0.15 | 0.20 | 0.30 | 0.41 | 0.51 | 0.61 | 0.91 | 1.22 | 1.52 | 3.04
 |  |  |  |  |  |  |  | 0.0022352 | 24 | 0.03 | 0.07 | 0.10 | 0.13 | 0.20 | 0.27 | 0.34 | 0.40 | 0.60 | 0.80 | 1.01 | 2.01
 |  |  |  |  |  |  |  | 0.0013208 | 22 | 0.02 | 0.04 | 0.06 | 0.08 | 0.12 | 0.16 | 0.20 | 0.24 | 0.36 | 0.48 | 0.59 | 1.19
 |  |  |  |  |  |  |  | 0.0008636 | 20 | 0.01 | 0.03 | 0.04 | 0.05 | 0.08 | 0.10 | 0.13 | 0.16 | 0.23 | 0.31 | 0.39 | 0.78
 |  |  |  |  |  |  |  | 0.0005334 | 18 | 0.01 | 0.02 | 0.02 | 0.03 | 0.05 | 0.06 | 0.08 | 0.10 | 0.14 | 0.19 | 0.24 | 0.48
 |  |  |  |  |  |  |  | 0.0003302 | 16 | 0.004953 | 0.01 | 0.01 | 0.02 | 0.03 | 0.04 | 0.05 | 0.06 | 0.09 | 0.12 | 0.15 | 0.30
 |  |  |  |  |  |  |  | 0.00020828 | 14 | 0.0031242 | 0.01 | 0.01 | 0.01 | 0.02 | 0.02 | 0.03 | 0.04 | 0.06 | 0.07 | 0.09 | 0.19
 |  |  |  |  |  |  |  | 0.00013208 | 12 | 0.0019812 | 0.0039624 | 0.01 | 0.01 | 0.01 | 0.02 | 0.02 | 0.02 | 0.04 | 0.05 | 0.06 | 0.12
 |  |  |  |  |  |  |  | 8.382e-05 | 10 | 0.0012573 | 0.0025146 | 0.0037719 | 0.01 | 0.01 | 0.01 | 0.01 | 0.02 | 0.02 | 0.03 | 0.04 | 0.08
 |  |  |  |  |  |  |  | 5.334e-05 | 8 | 0.0008001 | 0.0016002 | 0.0024003 | 0.0032004 | 0.0048006 | 0.01 | 0.01 | 0.01 | 0.01 | 0.02 | 0.02 | 0.05
 |  |  |  |  |  |  |  | 3.302e-05 | 6 | 0.0004953 | 0.0009906 | 0.0014859 | 0.0019812 | 0.0029718 | 0.0039624 | 0.004953 | 0.01 | 0.01 | 0.01 | 0.01 | 0.03

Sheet: Electronics Calculations
Drive Motor Stall Current | 5 | Amps
Weapon Motor Stall Current | 9 | Amps
Drive Coeffiecient | 0.2
Weapon Coefficient | 0.8
Match Time (min) | 3 | minutes
Number of Drive Motors | 2 | motors
Number of Weapon Motors | 1 | motors
Drive Amp Hourage | 0.1
Weapon Amp Hourage | 0.36
Min Battery Capacity | 460 | mAh
C-Rating Multiplier | 1.2
Total Max Draw | 19 | Amps
Min C Rating | 49.56521739 | C

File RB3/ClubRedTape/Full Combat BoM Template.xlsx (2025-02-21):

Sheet: BOM
DO NOT ENTER VALUES FOR COLUMNS HIGHLIGHTED GREEN
Overall Bot Value: |  | $14.46 | External Component $ Spent: | Railside $ Spent: | $33.89 | $0.00 | Total $ Spent: | $33.89
Category | Qty | Item | Ordering Specs | Vendor/Source | Link | Subsystem | Units per Package | Units per Bot | Provided by Railside? | Item Cost | What is the part for? | Unit Cost | Unit/Bot Cost | Total Cost
 | 1 | Fingertech Mini Power Switch |  | Itgresa | https://itgresa.com/product/mini-power-switch/ |  | 1 | 1 | yes | $7.99 | Robot disable switch | $7.99 | $7.99 | $7.99
 | 2 | Tattu 450 mAh 2S LiPo with XT30 |  | Amazon | https://www.amazon.com/TATTU-450mAh-Battery-Pack-H-Frame/dp/B07DTYN9QF?s=electronics |  | 2 | 1 | yes | $12.95 | Robot Power | $6.47 | $6.47 | $25.90
 |  | Drive motors | Self Supplied |  |  |  |  |  |  | $0.00 |  | $0.00 | $0.00 | $0.00
 |  | Receiver | Self Supplied |  |  |  |  |  |  | $0.00 |  | $0.00 | $0.00 | $0.00
Electronics |  | Drive esc (combined with receiver if using Malenki) | Self Supplied |  |  |  |  |  |  | $0.00 |  | $0.00 | $0.00 | $0.00
 |  | Weapon Motor | Self Supplied |  |  |  |  |  |  | $0.00 |  | $0.00 | $0.00 | $0.00
 |  | Weapon esc | Self Supplied |  |  |  |  |  |  | $0.00 |  | $0.00 | $0.00 | $0.00
 |  | Fuse | N.A. |  |  |  |  |  |  | $0.00 |  | $0.00 | $0.00 | $0.00
 |  |  |  |  |  |  |  |  |  | $0.00 |  | $0.00 | $0.00 | $0.00
 |  | Things like raw stock (AR 500, UHMW, 3D printer filament), and other stuff that makes up your robot structure go here |  |  |  |  |  |  |  | $0.00 |  | $0.00 | $0.00 | $0.00
Structure / Materials |  | Self Supplied |  |  |  |  |  |  |  | $0.00 |  | $0.00 | $0.00 | $0.00
 |  |  |  |  |  |  |  |  |  | $0.00 |  | $0.00 | $0.00 | $0.00
 |  | power transmission members (belts, pulleys), wheels, bushings/bearings
Power Transmission |  | Self Supplied |  |  |  |  |  |  |  | $0.00 |  | $0.00 | $0.00 | $0.00
 |  |  |  |  |  |  |  |  |  | $0.00 |  | $0.00 | $0.00 | $0.00
 |  | Screws, nuts, shoulder bolts go here |  |  |  |  |  |  |  | $0.00 |  | $0.00 | $0.00 | $0.00
 |  | Plastic screws, club supplied (1/2 inch) | (rough guesstimate of screw count, price not important) |  |  |  | X | 15 | yes | $0.00 | component adhesion | $0.00 | $0.00 | $0.00
Hardware (Fasteners) |  | Plastic screws, club supplied (3/4 inch) |  |  |  |  | X | 10 | yes | $0.00 |  | $0.00 | $0.00 | $0.00
 |  |  |  |  |  |  |  |  |  | $0.00 |  | $0.00 | $0.00 | $0.00
 |  |  |  |  |  |  |  |  |  | $0.00 |  | $0.00 | $0.00 | $0.00
 |  | Anything that doesnt fit into the above category |  |  |  |  |  |  |  | $0.00 |  | $0.00 | $0.00 | $0.00
 |  |  |  |  |  |  |  |  |  | $0.00 |  | $0.00 | $0.00 | $0.00
Misc. |  |  |  |  |  |  |  |  |  | $0.00 |  | $0.00 | $0.00 | $0.00
 |  |  |  |  |  |  |  |  |  | $0.00 |  | $0.00 | $0.00 | $0.00
 |  |  |  |  |  |  |  |  |  | $0.00 |  | $0.00 | $0.00 | $0.00
 |  |  |  |  |  |  |  |  |  | $0.00 |  | $0.00 | $0.00 | $0.00
 |  |  |  |  |  |  |  |  |  | $0.00 |  | $0.00 | $0.00 | $0.00
 |  |  |  |  |  |  |  |  |  | $0.00 |  | $0.00 | $0.00 | $0.00
 |  |  |  |  |  |  |  |  |  | $0.00 |  | $0.00 | $0.00 | $0.00
 |  |  |  |  |  |  |  |  |  | $0.00 |  | $0.00 | $0.00 | $0.00
 |  |  |  |  |  |  |  |  |  | $0.00 |  | $0.00 | $0.00 | $0.00
 |  |  |  |  |  |  |  |  |  | $0.00 |  | $0.00 | $0.00 | $0.00
 |  |  |  |  |  |  |  |  |  | $0.00 |  | $0.00 | $0.00 | $0.00
 |  |  |  |  |  |  |  |  |  | $0.00 |  | $0.00 | $0.00 | $0.00
 |  |  |  |  |  |  |  |  |  | $0.00 |  | $0.00 | $0.00 | $0.00
 |  |  |  |  |  |  |  |  |  | $0.00 |  | $0.00 | $0.00 | $0.00
 |  |  |  |  |  |  |  |  |  | $0.00 |  | $0.00 | $0.00 | $0.00
 |  |  |  |  |  |  |  |  |  | $0.00 |  | $0.00 | $0.00 | $0.00

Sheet: Physics Equations
Input yellow values | Green values will automatically be calculated
Battery
Cells | Voltage Level | Voltage Multiplier | Voltage (V)
2 | nominal | 3.7 | 7.4
Weapon Motor
Kv (rpm/V) | Throttle % | RPM | Kv (rad/s/V)
1100 | 100 | 8140 | 115.1917306
Weapon
Moment of Inertia (g*mm^2) | Diameter (in) | Weapon Reduction
1360078 | 9 | 1
MOI (kg*m^2) | RPM | (rev/s) | Angular Velocity (rad/s)
0.001360078 | 8140 | 135.6666667 | 852.4188067
Kinetic Energy (Joules) | Tip Speed (in/s) | Tip Speed (mph)
494.128457 | 3835.88463 | 217.9479903
Bite
Impactor Count | Max Impactor Angle (fraction) | Seconds per Hit (s) | Max Bite (in)
1 | 1 | 0.007371007371 | 0.4631340521
Drive Motor
RPM | Throttle % | RPM
800 | 100 | 800
Drive
Wheel Diameter (in) | Speed (in/min) | Speed (mph) | Speed (in/s)
1.5 | 3769.911184 | 3.569991652 | 62.83185307

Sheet: Wire Sizing Chart
 |  |  |  |  |  |  |  |  |  | Factor of Safety for Maximum Voltage Drop due to Wire Resistancce
AWG | Diameter (mm) | Area (mm^2) | Resistance Copper (ohm/1000m) | Resistance 1 inch (ohm) | System Voltage: | 7.4 | V |  |  | Wire Run Length (in)
 |  |  |  |  | Max V Drop: | 0.100 | V | Ohm/In | AWG | 1 | 2 | 3 | 4 | 6 | 8 | 10 | 12 | 18 | 24 | 30 | 60
 |  |  |  |  | Set Current: | 40 | A | 0.0033782 | 26 | 0.7 | 0.4 | 0.2 | 0.2 | 0.1 | 0.1 | 0.1 | 0.1 | 0.04111328189 | 0.03083496142 | 0.02466796914 | 0.01233398457
26 | 0.41 | 0.13 | 133 | 0.0033782 | Max Power Loss: | 4 | W | 0.0022352 | 24 | 1.1 | 0.6 | 0.4 | 0.3 | 0.2 | 0.1 | 0.1 | 0.1 | 0.1 | 0.04660283942 | 0.03728227153 | 0.01864113577
24 | 0.51 | 0.2 | 88 | 0.0022352 |  |  |  | 0.0013208 | 22 | 1.9 | 0.9 | 0.6 | 0.5 | 0.3 | 0.2 | 0.2 | 0.2 | 0.1 | 0.1 | 0.1 | 0.03154653745
22 | 0.64 | 0.33 | 52 | 0.0013208 |  |  |  | 0.0008636 | 20 | 2.9 | 1.4 | 1.0 | 0.7 | 0.5 | 0.4 | 0.3 | 0.2 | 0.2 | 0.1 | 0.1 | 0.04824764551
20 | 0.81 | 0.5 | 34 | 0.0008636 |  |  |  | 0.0005334 | 18 | 4.7 | 2.3 | 1.6 | 1.2 | 0.8 | 0.6 | 0.5 | 0.4 | 0.3 | 0.2 | 0.2 | 0.1
18 | 1 | 0.82 | 21 | 0.0005334 |  |  |  | 0.0003302 | 16 | 7.6 | 3.8 | 2.5 | 1.9 | 1.3 | 0.9 | 0.8 | 0.6 | 0.4 | 0.3 | 0.3 | 0.1
16 | 1.3 | 1.3 | 13 | 0.0003302 |  |  |  | 0.00020828 | 14 | 12.0 | 6.0 | 4.0 | 3.0 | 2.0 | 1.5 | 1.2 | 1.0 | 0.7 | 0.5 | 0.4 | 0.2
14 | 1.6 | 2.1 | 8.2 | 0.00020828 |  |  |  | 0.00013208 | 12 | 18.9 | 9.5 | 6.3 | 4.7 | 3.2 | 2.4 | 1.9 | 1.6 | 1.1 | 0.8 | 0.6 | 0.3
12 | 2.1 | 3.3 | 5.2 | 0.00013208 |  |  |  | 8.382e-05 | 10 | 29.8 | 14.9 | 9.9 | 7.5 | 5.0 | 3.7 | 3.0 | 2.5 | 1.7 | 1.2 | 1.0 | 0.5
10 | 2.6 | 5.3 | 3.3 | 8.382e-05 |  |  |  | 5.334e-05 | 8 | 46.9 | 23.4 | 15.6 | 11.7 | 7.8 | 5.9 | 4.7 | 3.9 | 2.6 | 2.0 | 1.6 | 0.8
8 | 3.3 | 8.3 | 2.1 | 5.334e-05 |  |  |  | 3.302e-05 | 6 | 75.7 | 37.9 | 25.2 | 18.9 | 12.6 | 9.5 | 7.6 | 6.3 | 4.2 | 3.2 | 2.5 | 1.3
6 | 4.1 | 13.3 | 1.3 | 3.302e-05 |  |  |  |  |  | Voltage Drop due to Wire Resistance
 |  |  |  |  |  |  |  |  |  | Wire Run Length (in)
 |  |  |  |  |  |  |  | Ohm/In | AWG | 1 | 2 | 3 | 4 | 6 | 8 | 10 | 12 | 18 | 24 | 30 | 60
 |  |  |  |  |  |  |  | 0.0033782 | 26 | 0.14 | 0.27 | 0.41 | 0.54 | 0.81 | 1.08 | 1.35 | 1.62 | 2.43 | 3.24 | 4.05 | 8.11
 |  |  |  |  |  |  |  | 0.0022352 | 24 | 0.09 | 0.18 | 0.27 | 0.36 | 0.54 | 0.72 | 0.89 | 1.07 | 1.61 | 2.15 | 2.68 | 5.36
 |  |  |  |  |  |  |  | 0.0013208 | 22 | 0.05 | 0.11 | 0.16 | 0.21 | 0.32 | 0.42 | 0.53 | 0.63 | 0.95 | 1.27 | 1.58 | 3.17
 |  |  |  |  |  |  |  | 0.0008636 | 20 | 0.03 | 0.07 | 0.10 | 0.14 | 0.21 | 0.28 | 0.35 | 0.41 | 0.62 | 0.83 | 1.04 | 2.07
 |  |  |  |  |  |  |  | 0.0005334 | 18 | 0.02 | 0.04 | 0.06 | 0.09 | 0.13 | 0.17 | 0.21 | 0.26 | 0.38 | 0.51 | 0.64 | 1.28
 |  |  |  |  |  |  |  | 0.0003302 | 16 | 0.01 | 0.03 | 0.04 | 0.05 | 0.08 | 0.11 | 0.13 | 0.16 | 0.24 | 0.32 | 0.40 | 0.79
 |  |  |  |  |  |  |  | 0.00020828 | 14 | 0.01 | 0.02 | 0.02 | 0.03 | 0.05 | 0.07 | 0.08 | 0.10 | 0.15 | 0.20 | 0.25 | 0.50
 |  |  |  |  |  |  |  | 0.00013208 | 12 | 0.01 | 0.01 | 0.02 | 0.02 | 0.03 | 0.04 | 0.05 | 0.06 | 0.10 | 0.13 | 0.16 | 0.32
 |  |  |  |  |  |  |  | 8.382e-05 | 10 | 0.0033528 | 0.01 | 0.01 | 0.01 | 0.02 | 0.03 | 0.03 | 0.04 | 0.06 | 0.08 | 0.10 | 0.20
 |  |  |  |  |  |  |  | 5.334e-05 | 8 | 0.0021336 | 0.0042672 | 0.01 | 0.01 | 0.01 | 0.02 | 0.02 | 0.03 | 0.04 | 0.05 | 0.06 | 0.13
 |  |  |  |  |  |  |  | 3.302e-05 | 6 | 0.0013208 | 0.0026416 | 0.0039624 | 0.01 | 0.01 | 0.01 | 0.01 | 0.02 | 0.02 | 0.03 | 0.04 | 0.08

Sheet: Electronics Calculations
Drive Motor Stall Current | 2.2 | Amps
Weapon Motor Stall Current | 9.9 | Amps
Drive Coeffiecient | 0.2
Weapon Coefficient | 0.8
Match Time (min) | 3 | minutes
Number of Drive Motors | 2 | motors
Number of Weapon Motors | 1 | motors
Drive Amp Hourage | 0.044
Weapon Amp Hourage | 0.396
Min Battery Capacity | 440 | mAh
C-Rating Multiplier | 1.5
Total Max Draw | 14.3 | Amps
Min C Rating | 48.75 | C

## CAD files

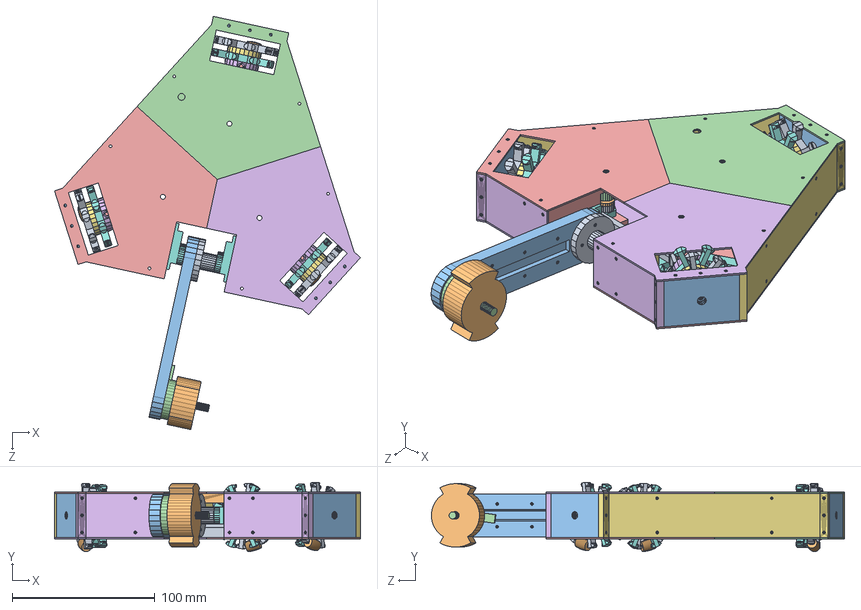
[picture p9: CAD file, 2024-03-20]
RB1/ClubRedTape/SolidworksFiles/Parts/OMNI-A-0000TLA.SLDASM
214.5 x 48.6 x 289.7 mm
OMNI-P-0200Chassis
OMNI-P-0201FrameSpacerEdge x 2
OMNI-P-0202FrameSpacerFlat
OMNI-P-0203FrameSpacerTall x 3
OMNI-P-0204ServoHolder x 2
OMNI-P-0205SideWallFrontThin x 2
OMNI-P-0206SideWallThin x 2
OMNI-P-0207StrutA x 4
OMNI-P-0208StrutB
OMNI-P-0209StrutC
OMNI-P-0210WheelWallThin x 3
OMNI-P-0211TopWall1 x 2
OMNI-P-0212TopWall2 x 2
OMNI-P-0213TopWall3 x 2
OMNI-P-0102REF_Servo_BOTTOM x 2
OMNI-P-0103REF_Servo_TOP x 2
OMNI-P-0403ArmMount
OMNI-P-0402Blade
OMNI-P-0403BladeArm
OMNI-P-0104REF_Motor
OMNI-P-0100REF_N20 x 3
OMNI-P-0301Omniwheel_M3ShaftCoupling_inset x 3
OMNI-P-0302Omniwheel_T3_3_Hub_Spacer x 3
OMNI-P-0303Omniwheel_T3_3_Hub1 x 3
OMNI-P-0304Omniwheel_T3_3_Hub2 x 3
OMNI-P-0305Omniwheel_T3_Roller_Plastic_W x 3

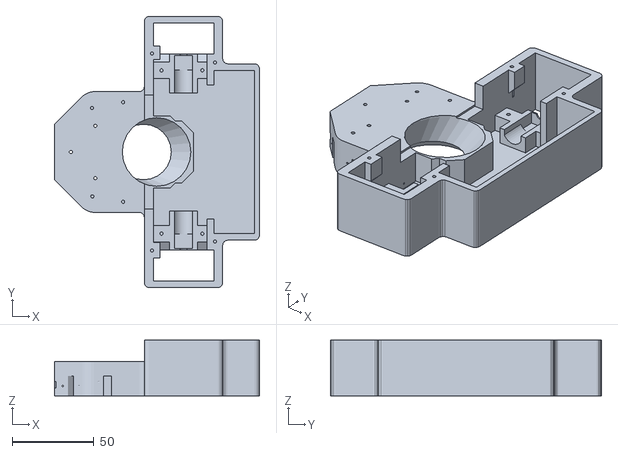
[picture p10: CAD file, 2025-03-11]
RB3/CAD/STL/MainChassis.stl
125.5 x 166.0 x 34.0

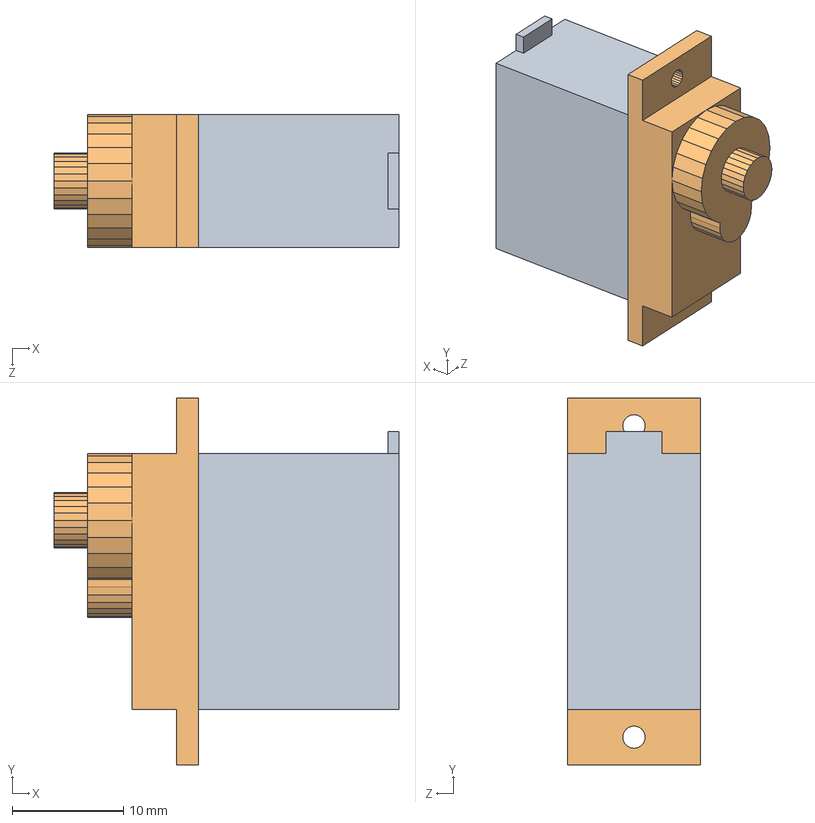
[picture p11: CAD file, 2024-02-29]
RB1/ClubRedTape/SolidworksFiles/Parts/OMNI-A-0101ServoComplete.SLDASM
31.0 x 33.0 x 12.0 mm
OMNI-P-0102REF_Servo_BOTTOM
OMNI-P-0103REF_Servo_TOP

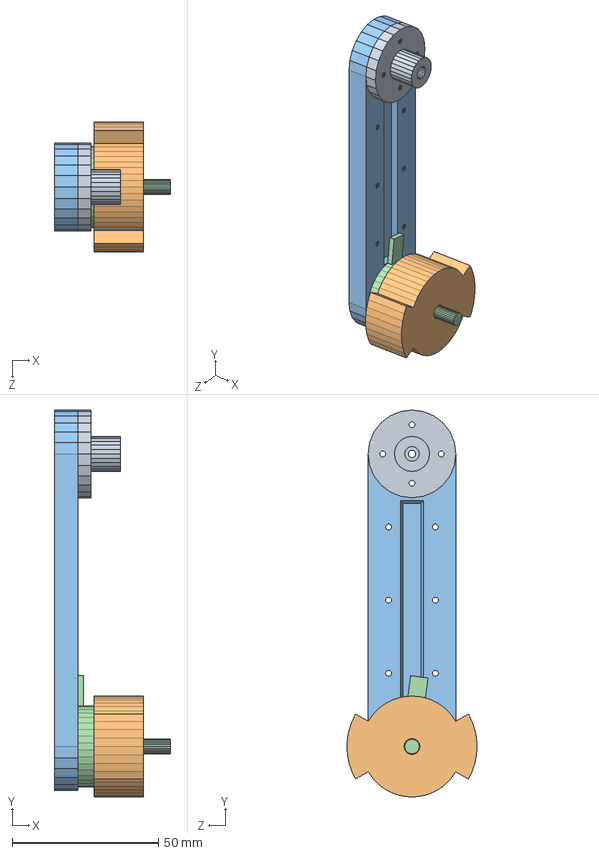
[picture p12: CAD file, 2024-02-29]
RB1/ClubRedTape/SolidworksFiles/Parts/OMNI-A-0400Weapon.SLDASM
39.7 x 132.2 x 44.5 mm
OMNI-P-0403ArmMount
OMNI-P-0402Blade
OMNI-P-0403BladeArm
OMNI-P-0104REF_Motor

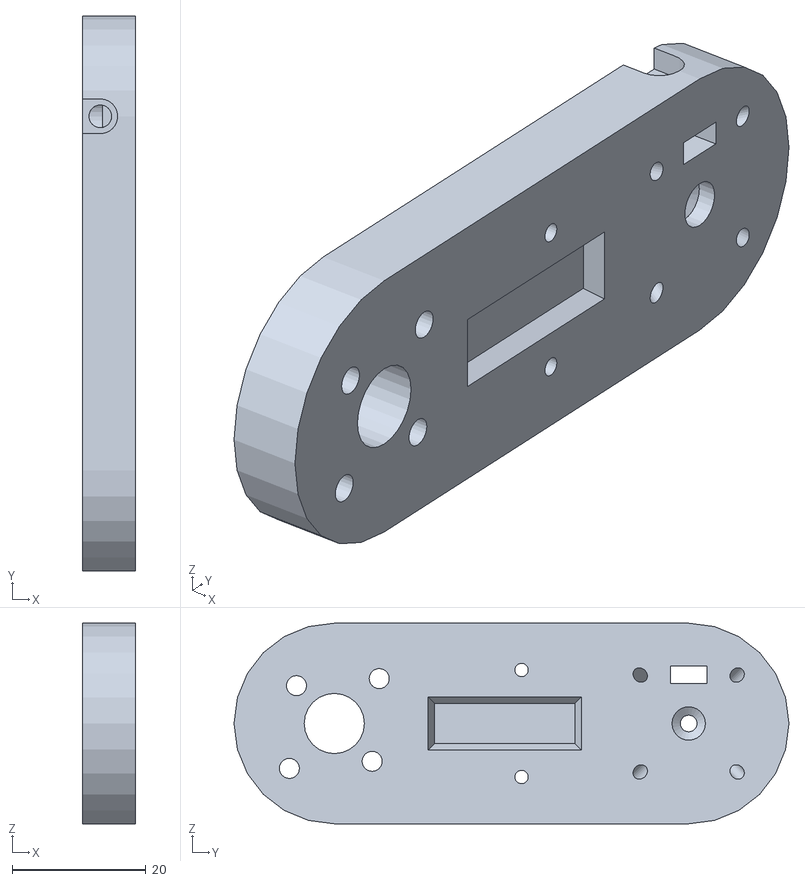
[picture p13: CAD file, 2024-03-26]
RB1/CAD/STL/BladeArmShortAngledKey.stl
8.00 x 83.0 x 30.0

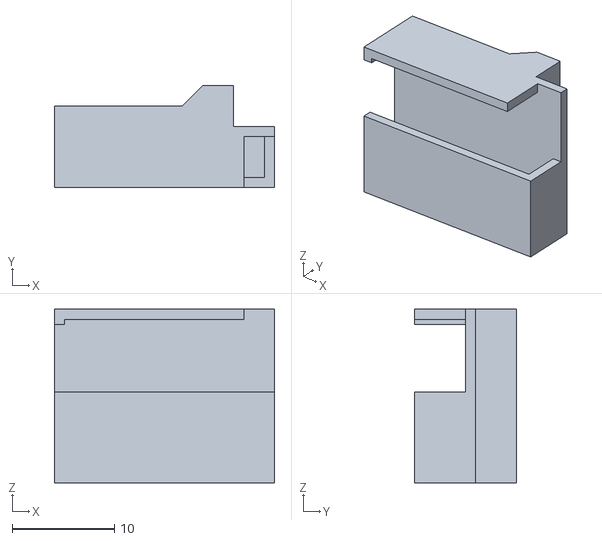
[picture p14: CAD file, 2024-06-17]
RB1/CAD/STL/Camera/TransmitterHolder.stl
21.5 x 10.0 x 17.0

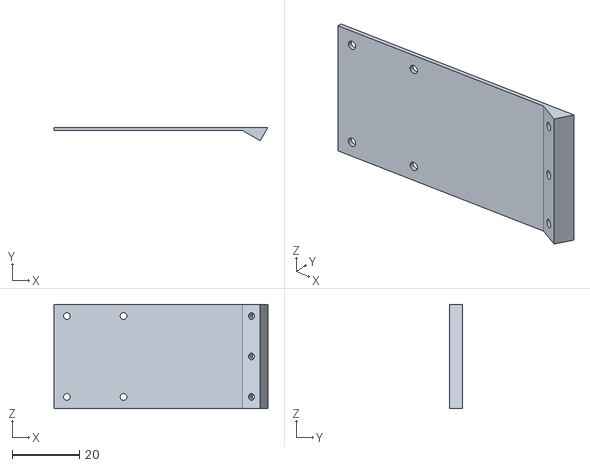
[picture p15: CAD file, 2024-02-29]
RB1/CAD/STL/Depricated/SideWallFrontThin.stl
63.5 x 4.00 x 31.0

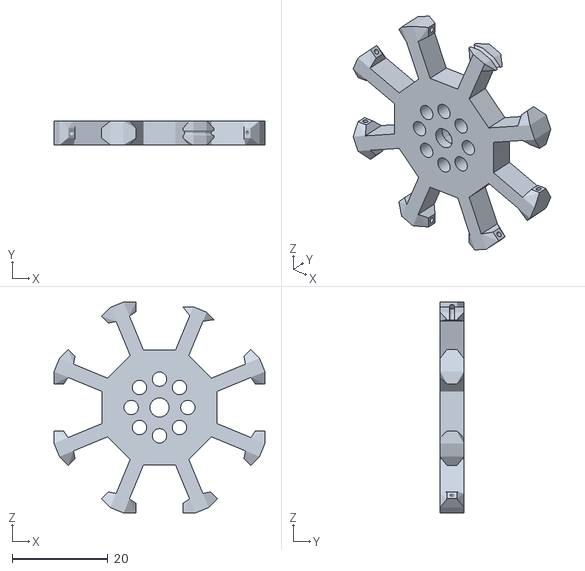
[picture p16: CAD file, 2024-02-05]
RB1/CAD/STL/Wheels/Depricated/Omniwheel_T3-1_Hub.stl
44.0 x 5.00 x 44.0

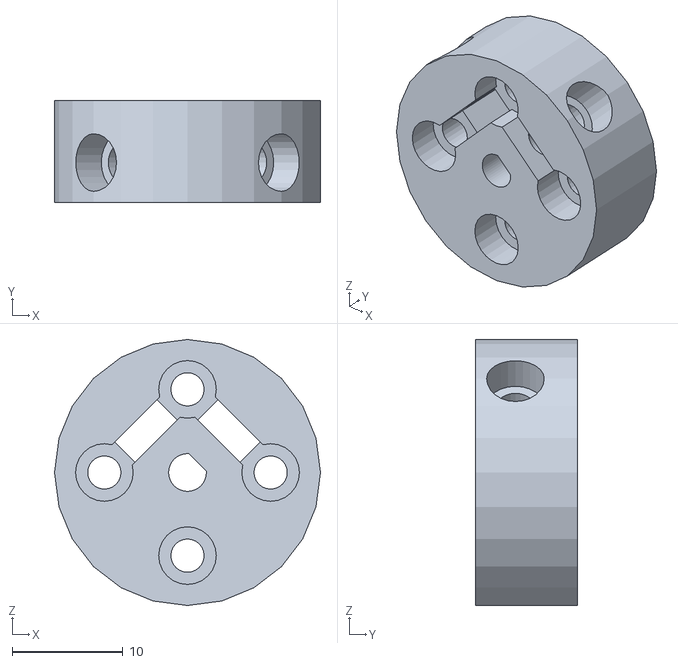
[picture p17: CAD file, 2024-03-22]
RB1/CAD/STL/Wheels/M3ShaftCoupling_inset_longer.stl
24.0 x 9.20 x 24.0

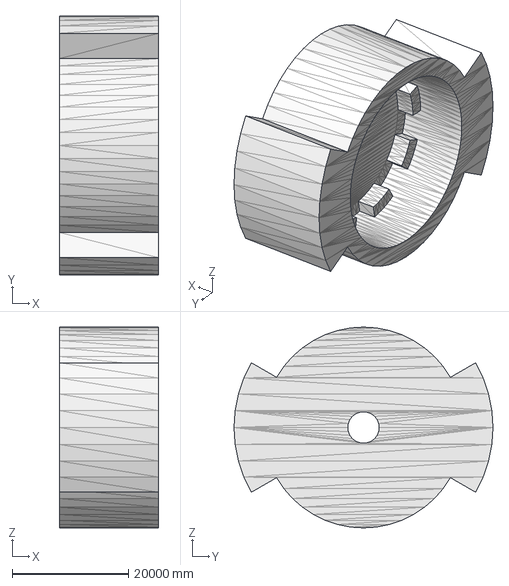
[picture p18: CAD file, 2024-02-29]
RB1/ClubRedTape/ExportExperiments/Unnamed-SinglePart001001.step
17000.0 x 44500.0 x 34500.0 mm

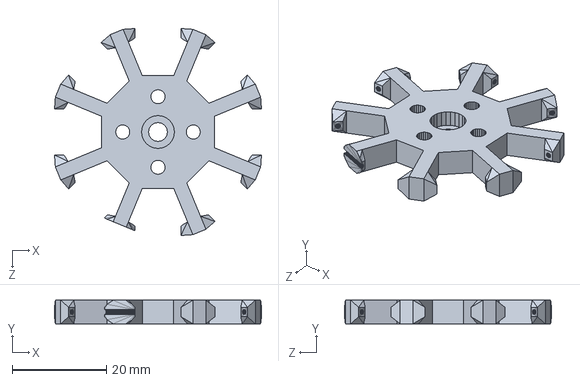
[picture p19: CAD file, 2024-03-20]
RB1/ClubRedTape/SolidworksFiles/Parts/OMNI-P-0303Omniwheel_T3_3_Hub1.SLDPRT
44.0 x 5.00 x 44.0 mm

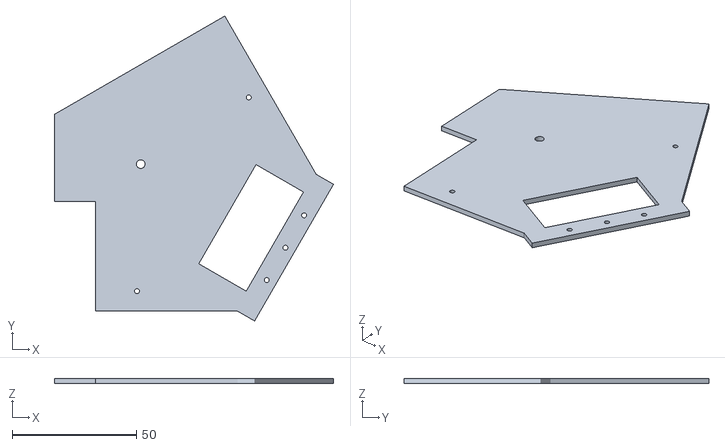
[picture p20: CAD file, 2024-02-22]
RB1/ClubRedTape/STL/Depricated/Cover_C.stl
112.1 x 122.5 x 2.00

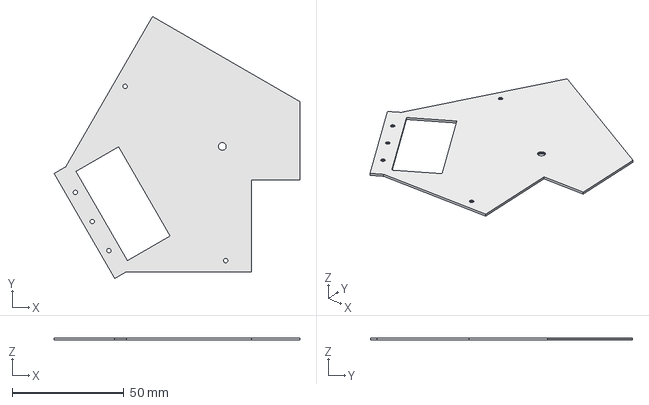
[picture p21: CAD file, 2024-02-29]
RB1/ClubRedTape/STL/TopWall2.step
109.8 x 117.0 x 1.00 mm

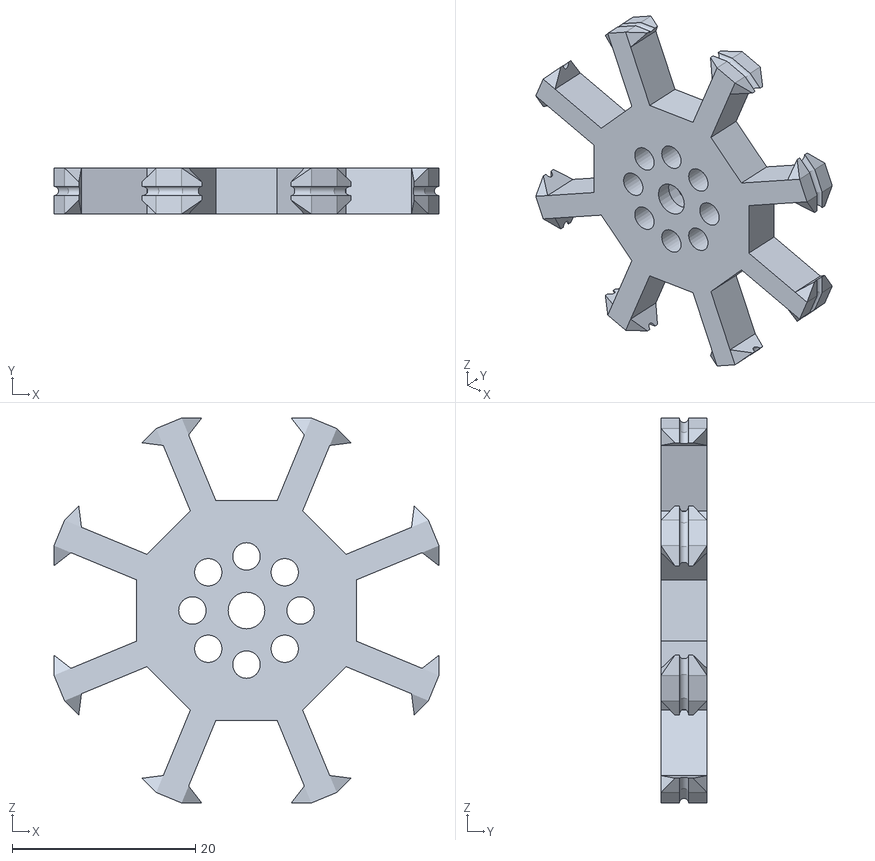
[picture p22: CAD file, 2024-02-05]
RB1/ClubRedTape/STL/Wheels/Depricated/Omniwheel_T3_Hub.stl
42.0 x 5.00 x 42.0

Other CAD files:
RB1/ClubRedTape/SolidworksFiles/Parts/OMNI-A-0300Wheel.SLDASM
RB1/ClubRedTape/SolidworksFiles/Parts/OMNI-A-0200Lid.SLDASM
RB3/CAD/STL/MainChassis_W_CustomInfill.3mf
RB1/ClubRedTape/STL/Wheels/M3ShaftCoupling_inset.stl
RB1/CAD/STL/ArmMountAngled.stl
RB1/CAD/STL/ArmMountAngledKey.stl
RB1/CAD/STL/ArmMountAngledKey13.5.stl
RB1/CAD/STL/ArmMountAngledKeyShort.stl
RB1/CAD/STL/Blade.stl
RB1/CAD/STL/BladeArmAngled.stl
RB1/CAD/STL/BladeArmAngledKey.stl
RB1/CAD/STL/BladeLock.stl
RB1/CAD/STL/BladeLockWide.stl
RB1/CAD/STL/Camera/CameraPartsPlate.stl
RB1/CAD/STL/Camera/PivotLeft.stl
RB1/CAD/STL/Camera/PivotRight.stl
RB1/CAD/STL/Camera/SensorHolder.stl
RB1/CAD/STL/ChassisWithScrews.stl
RB1/CAD/STL/Depricated/ArmMount.stl
RB1/CAD/STL/Depricated/BladeArm.stl
RB1/CAD/STL/Depricated/BladeArmA.stl
RB1/CAD/STL/Depricated/BladeArmB.stl
RB1/CAD/STL/Depricated/Chassis.stl
RB1/CAD/STL/Depricated/Cover_A.stl
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

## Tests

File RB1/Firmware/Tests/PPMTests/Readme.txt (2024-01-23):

This test program is for getting PPM decoding to work with the STM32, so it can use the RFM69HW to transmit messages from any RC control surface.

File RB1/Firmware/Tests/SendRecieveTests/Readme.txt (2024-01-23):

This test program is meant to try out the features of the RFM69HW radio module. This was originally made with the creation of LittleBuddy, an ISkipper based on the STM32.

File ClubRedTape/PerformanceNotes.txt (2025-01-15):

Robot navegated OK
Weapon was too small
Servo gears could not take the stress of the weapon

Bigger blade = better (further reach, bigger hits)

Compact the electronics
(all really needed: ESP32, DRV883x1, Mini360Buck)

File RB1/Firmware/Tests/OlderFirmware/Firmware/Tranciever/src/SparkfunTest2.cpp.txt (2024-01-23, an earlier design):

// RFM69HCW Example Sketch
// Send serial input characters from one RFM69 node to another
// Based on RFM69 library sample code by Felix Rusu
// http://LowPowerLab.com/contact
// Modified for RFM69HCW by Mike Grusin, 4/16

// This sketch will show you the basics of using an
// RFM69HCW radio module. SparkFun's part numbers are:
// 915MHz: https://www.sparkfun.com/products/12775
// 434MHz: https://www.sparkfun.com/products/12823

// See the hook-up guide for wiring instructions:
// https://learn.sparkfun.com/tutorials/rfm69hcw-hookup-guide

// Uses the RFM69 library by Felix Rusu, LowPowerLab.com
// Original library: https://www.github.com/lowpowerlab/rfm69
// SparkFun repository: https://github.com/sparkfun/RFM69HCW_Breakout

// Include the RFM69 and SPI libraries:

#include <Arduino.h>
#include <RFM69.h>
#include <SPI.h>
#include "SparkfunTest.h"

// Addresses for this node. CHANGE THESE FOR EACH NODE!

#define NETWORKID     0   // Must be the same for all nodes
#define MYNODEID      2   // My node ID
#define TONODEID      1   // Destination node ID

// RFM69 frequency, uncomment the frequency of your module:

//#define FREQUENCY   RF69_433MHZ
#define FREQUENCY     RF69_915MHZ

// AES encryption (or not):

#define ENCRYPT       true // Set to "true" to use encryption
#define ENCRYPTKEY    "TOPSECRETPASSWRD" // Use the same 16-byte key on all nodes

// Use ACKnowledge when sending messages (or not):

#define USEACK        true // Request ACKs or not

// Packet sent/received indicator LED (optional):

#define LED           LED_BUILTIN // LED positive pin
#define GND           8 // LED ground pin

// Create a library object for our RFM69HCW module:

RFM69 radio;

//support functions:
void Blink(byte PIN, int DELAY_MS)
// Blink an LED for a given number of ms
{
  digitalWrite(PIN,LOW);
  delay(DELAY_MS);
  digitalWrite(PIN,HIGH);
}

void HandleA(void)
{

    Blink(LED, 10);
}

void setupFunc()
{
  // Open a serial port so we can send keystrokes to the module:

  Serial.begin(9600);
  Serial.print("Node ");
  Serial.print(MYNODEID,DEC);
  Serial.println(" ready");  

  // Set up the indicator LED (optional):

  pinMode(LED,OUTPUT);
  digitalWrite(LED,HIGH);
  pinMode(GND,OUTPUT);
  digitalWrite(GND,LOW);

  // Initialize the RFM69HCW:
  radio.setCS(PA4);  //uncomment this if using Pro Micro
  radio.setIrq(PB4);
  //radio.spyMode(true);
  //radio.setIsrCallback(&HandleA);
  radio.initialize(FREQUENCY, MYNODEID, NETWORKID);
  radio.setHighPower(); // Always use this for RFM69HCW

  // Turn on encryption if desired:

  if (ENCRYPT)
    radio.encrypt(ENCRYPTKEY);
}

void loopFunc(int Clicked)
{
  // Set up a "buffer" for characters that we'll send:

  static char sendbuffer[62];
  static int sendlength = 0;

  // SENDING

  // In this section, we'll gather serial characters and
  // send them to the other node if we (1) get a carriage return,
  // or (2) the buffer is full (61 characters).

  // If there is any serial input, add it to the buffer:

  if (Serial.available() > 0)
  {
    char input = Serial.read();

    if (input != '\r') // not a carriage return
    {
      Serial.print(input);
      sendbuffer[sendlength] = input;
      sendlength++;
    }

    // If the input is a carriage return, or the buffer is full:

    if ((input == '\r') || (sendlength == 61)) // CR or buffer full
    {
      // Send the packet!

      Serial.print("sending to node ");
      Serial.print(TONODEID, DEC);
      Serial.print(", message [");
      for (byte i = 0; i < sendlength; i++)
        Serial.print(sendbuffer[i]);
      Serial.println("]");

      // There are two ways to send packets. If you want
      // acknowledgements, use sendWithRetry():

      if (USEACK)
      {
        if (radio.sendWithRetry(TONODEID, sendbuffer, sendlength))
          Serial.println("ACK received!");
        else
          Serial.println("no ACK received");
      }

      // If you don't need acknowledgements, just use send():

      else // don't use ACK
      {
        radio.send(TONODEID, sendbuffer, sendlength);
      }

      sendlength = 0; // reset the packet
      Blink(LED,10);
    }
  }

    char sendBuffer2[] = {"Hello, there"};
    if(Clicked)
        radio.send(TONODEID, sendBuffer2, sizeof(sendBuffer2));

  // RECEIVING

  // In this section, we'll check with the RFM69HCW to see
  // if it has received any packets:

  if (radio.receiveDone()) // Got one!
  {
    // Print out the information:

    Serial.print("received from node ");
    Serial.print(radio.SENDERID, DEC);
    Serial.print(", message [");

    // The actual message is contained in the DATA array,
    // and is DATALEN bytes in size:

    for (byte i = 0; i < radio.DATALEN; i++)
      Serial.print((char)radio.DATA[i]);

    // RSSI is the "Receive Signal Strength Indicator",
    // smaller numbers mean higher power.

    Serial.print("], RSSI ");
    Serial.println(radio.RSSI);

    // Send an ACK if requested.
    // (You don't need this code if you're not using ACKs.)

    if (radio.ACKRequested())
    {
      radio.sendACK();
      Serial.println("ACK sent");
    }
    Blink(LED,10);
  }
}

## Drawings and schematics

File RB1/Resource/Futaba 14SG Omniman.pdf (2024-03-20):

SB

### SA Turn Response tune [6] Motor ramp tune [7]

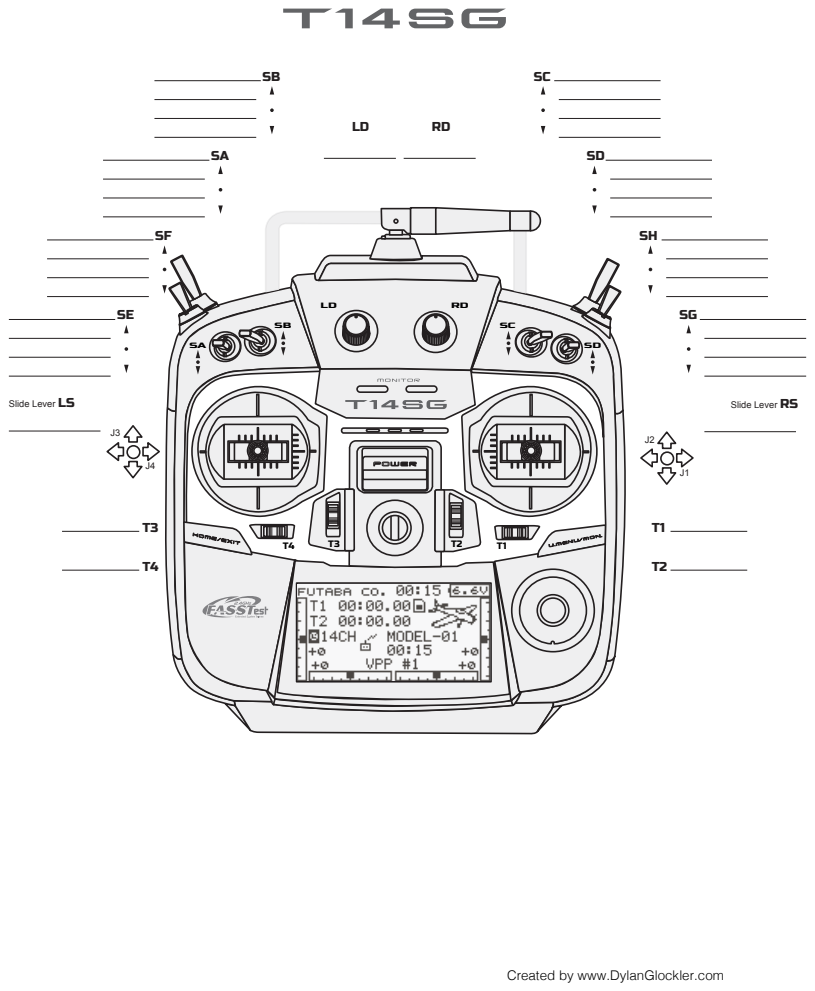
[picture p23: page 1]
Slide Lever LS; Slide Lever RS

Created by www.DylanGlockler.com

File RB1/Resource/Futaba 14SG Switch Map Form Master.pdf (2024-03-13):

SB

SA

Slide Lever LS; Slide Lever RS

Created by www.DylanGlockler.com

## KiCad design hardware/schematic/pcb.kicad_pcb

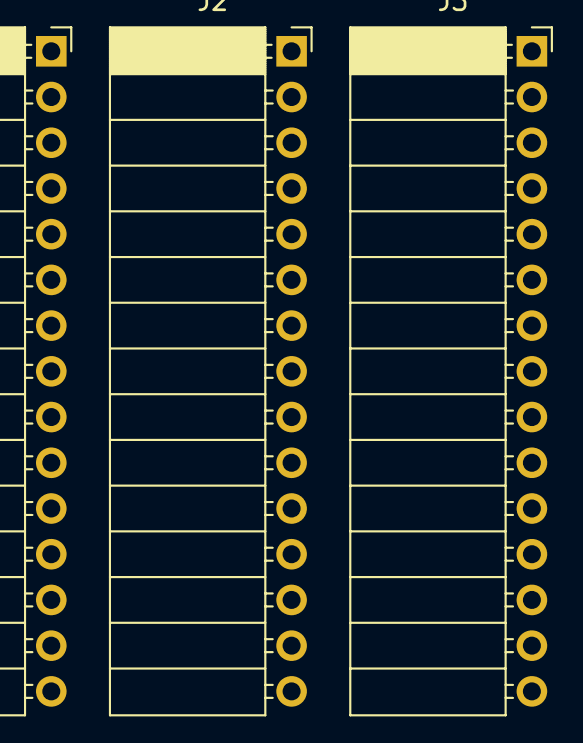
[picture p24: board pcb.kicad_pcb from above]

Board: 2 copper layers, 3 parts (0 on the bottom side), 10 nets, no tracks yet.

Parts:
J1: L; PinSocket_1x15_P2.54mm_Horizontal
J2: R; PinSocket_1x15_P2.54mm_Horizontal
J3: IR; PinSocket_1x15_P2.54mm_Horizontal

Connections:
unnamed: J1.12 (5V), J3.11 (VCC)
unnamed: J1.10 (A6), J3.10 (D8)
unnamed: J2.11 (D2), J3.3 (D1)
unnamed: J2.9 (D4), J3.4 (D2)
unnamed: J2.6 (D7), J3.5 (D3)
unnamed: J2.5 (D8), J3.6 (D4)
unnamed: J2.3 (D10), J3.7 (D5)
unnamed: J2.2 (D11), J3.8 (D6)
unnamed: J2.1 (D12), J3.9 (D7)
unnamed: J2.12 (GND), J3.1 (GND)

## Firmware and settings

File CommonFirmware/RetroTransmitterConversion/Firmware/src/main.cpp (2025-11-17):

#include <Arduino.h>
#include <SPI.h>


#include "configuration.h"
#include "RFM69HW.h"


RadioHandler* rh = nullptr;


void setup() {

    Serial.begin(115200);

#ifdef USING_ESP32
    SPI.begin(PIN_SCK, PIN_MISO, PIN_MOSI);
#elif USING_STM32
    SPI.begin();
#endif



    rh = new RadioHandler();

    rh->begin(&SPI, PIN_NSS, PIN_RESET, PIN_ISR, MYNODEID, NETWORKID, ENCRYPTKEY);




}

bool flipper = false;
int last_ms = 0;
void loop() {


    if(millis() - last_ms >= 10) {
        last_ms = millis();
        flipper = !flipper;

        Serial.printf("Send\n");


        Packet pt = {};
        ptype ptt = CONTROL_TYPE;
        if(flipper) {


            pt.control.analog_channels[0] = 67;
            ptt = CONTROL_TYPE;            

        } else {

            pt.response.battery_voltage = 6.7;
            ptt = RESPONSE_TYPE;
        }

        rh->sendPacket(&pt, ptt, TONODEID, false);



    }


    Packet pt = {};
    ptype ptt = {};
    if(rh->checkForPackets(pt, ptt)) {
        //nothing for now.
        if(ptt == CONTROL_TYPE) {
            Serial.printf("Analog channel 0: %d\n", pt.control.analog_channels[0]);
        } else {
            Serial.printf("Battery voltage 0: %f\n", pt.response.battery_voltage);
        }
        
        
    }




}

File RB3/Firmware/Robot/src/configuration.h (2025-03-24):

//Configuration
#pragma once


////////RADIO SETTINGS////////

//espnow
#define NETWORKID           4   // Must be the same for all nodes
//custom MAC addresses
#define PEER_ADDRESS {0x30, 0xAE, 0xA4, 0x07, 0x0D, 0x64}
#define MY_ADDRESS {0xA0, 0x0E, 0x04, 0x0F, 0xFD, 0x64}


#define ENCRYPT       false // Set to "true" to use encryption
#define ENCRYPTKEY_S {0xA0,0xA0,0xFF,0x00,0xFF,0xA0,0xA0,0xA0,0xFF,0x45,0xA0,0xA0,0x26,0x20,0x43,0xA0}
#define ENCRYPTKEY_P    "HOTCRYSTALBABESS" //"TOPSECRETPASSWRD" // Use the same 16-byte key on all nodes


////////////////PPM SETTINGS////////////////

//for processing and sending out remote control channel data

//how many analog channels we have
#define ANALOG_CHANNEL_CNT 8
//how many grouped digital channels we have (2 digital inputs per channel, due to how futaba remotes work)
#define DIGITAL_CHANNEL_CNT 4

#define CHANNEL_COUNT ANALOG_CHANNEL_CNT + DIGITAL_CHANNEL_CNT

//the range of the normalized analog values (mapped between [0,this], exclusive? or --inclusive?)
//adding detune will not affect these values
#define NORMAL_MIN 0
#define NORMAL_MAX 512



//something
#define KAKAJAMANGA

//for the STM32, random pins are used for testing: this part of the code will be used on the ESP32


//no radio transmission for 1 second, robot shuts off
#define KEEPALIVE_TIMEOUT_MS 1000

//slope mapping based on experimetnal data and resistor values (TODO: make this parametric)
#define VOLTMETER_SLOPE 0.0029
#define VOLTMETER_OFFSET 0.4129

//h-bridge operation:
//HI-HI is break
//LO-LO is no connection
//HI-LO is dir 1
//LO-HI is dir 2


//DRIVEBASE PINS
#define MOTOR_1A_PIN 0
#define MOTOR_1B_PIN 1
#define MOTOR_2A_PIN 2
#define MOTOR_2B_PIN 3

#define MOTOR_SLEEP_PIN 4


//WEAPON PINS
#define ESC_PIN 8

//ENCODER PINS
#define MOTOR_1_ENCA 10
#define MOTOR_1_ENCB 7
#define MOTOR_2_ENCA 6
#define MOTOR_2_ENCB 5




//////////////control surface mapping
//these are not directly used by the transmitter, but are the indexes of the transmitter packet that we use to check for this stuff

#ifdef FIXED_TRANSMITTER
#define VERTICAL_LEFT 3
#define HORIZONTAL_LEFT 4
#define VERTICAL_RIGHT 2
#define HORIZONTAL_RIGHT 1
#define PADDLE_LEFT 5
#define PADDLE_RIGHT 6
#define TUNER_LEFT 7
#define TUNER_RIGHT 8

//todo: these mappings are wrong
#define DIG_SA 1
#define DIG_POI 2
#define DIG_SC 3
#define DIG_FS 4
#define DIG_ATT 5
#define DIG_SF 6
#define DIG_DRRUD 7
#define DIG_SH 8
#else

#define VERTICAL_RIGHT 1
#define HORIZONTAL_RIGHT 0
#define VERTICAL_LEFT 2
#define HORIZONTAL_LEFT 3
#define PADDLE_LEFT 4
#define PADDLE_RIGHT 5
#define TUNER_LEFT 6
#define TUNER_RIGHT 7

#define DIG_SA 0
#define DIG_POI 1
#define DIG_SC 2
#define DIG_FS 3
#define DIG_ATT 4
#define DIG_SF 5
#define DIG_DRRUD 6
#define DIG_SH 7

#endif


// //analog
// #define X_IN 0
// #define Y_IN 1
// #define TURN_IN 3
// #define SERVO_IN 2
// #define ESC_IN 4
// #define SERVO_MIN_IN 5
// #define TURN_RAMP_TUNE 6
// #define MOTOR_RAMP_TUNE 7

// //digital
// #define FLIPOVER_IN 1//5
// #define ESC_REVERSE_IN 0//4
// #define TWO_MODE_IN 7
// #define TWO_SELECT_IN 6
// #define MASTER_ENABLE 2

////////////////////normalization

//the max speed of the motor in both directions
#define MOTOR_RPM_MAX 400


//analog servos have slightly different values that are mapped from the normalized range
#define SERVO_1_MS_MIN 500//600 //500 //604
#define SERVO_1_MS_MAX 2500//2200 //2500 //2200

#define SERVO_2_MS_MIN 500//660 //500 //660
#define SERVO_2_MS_MAX 2500//2100 //2500 //2100
//normalized range, shared between both servos
#define SERVO_MIN 0
#define SERVO_MAX 512


//number of magnets in the motor (for erpm measurements, only used in dshot mode)
#define MOTOR_POLE_COUNT 14


//backwards is 48-1047,
//forwards is 1048-2047
//dshot speeds (better than PWM, but only works with the dshot library)
//full speed in 3D mode
#define ESC_SPEED_MIN_R 48
#define ESC_SPEED_MAX_R 1047
#define ESC_SPEED_MIN_F 1048
#define ESC_SPEED_MAX_F 2047

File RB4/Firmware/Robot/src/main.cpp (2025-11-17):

#include <Arduino.h>

#include <esp_now.h>
#include <esp_wifi.h>
#include <Wifi.h>
#include <DShotRMT.h>

#include "configuration.h"
#include "TimerTick.h"

#include "Robot.h"


#include <Adafruit_NeoPixel.h>

RobotHandler* robot = nullptr;

//esp32 supermini plus has a neopixel on pin 8.
//it shares this pin with a traditional LED (1 == ON)
//Adafruit_NeoPixel pixels(1, 8, NEO_GRB + NEO_KHZ800);

void setup()
{
    Serial.begin(115200);

    // pinMode(SLEEP_PIN, OUTPUT);
    // digitalWrite(SLEEP_PIN, 1);
    // pinMode(5, OUTPUT);
    // pinMode(6, OUTPUT);
    // digitalWrite(5, 0);
    // digitalWrite(6, 0);

    // pinMode(9, OUTPUT);
    // pinMode(7, OUTPUT);
    // digitalWrite(9, 0);

    // while(1) {
    //     digitalWrite(7, 0);
    //     digitalWrite(9, 1);
    //     delay(1000);
    //     digitalWrite(9, 0);
    //     digitalWrite(7, 1);
    //     delay(1000);
    // }


    robot = new RobotHandler();

}


void loop()
{
    robot->update();


}

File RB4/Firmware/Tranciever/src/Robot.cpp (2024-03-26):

#include <Arduino.h>
#include <math.h>

#ifdef USING_ESP32
#include <ESP32Servo.h>
#include <DShotRMT.h>
#endif

#include "Controller.h"
#include "ESPRadio.h"
#include "configuration.h"
#include "Robot.h"


#ifndef IS_CONTROLLER



float mapf(float x, float in_min, float in_max, float out_min, float out_max) {
    const float run = in_max - in_min;
    if(run == 0.0){
        log_e("map(): Invalid input range, min == max");
        return -1; // AVR returns -1, SAM returns 0
    }
    const float rise = out_max - out_min;
    const float delta = x - in_min;
    return (delta * rise) / run + out_min;
}


RobotHandler::RobotHandler()
{

    //init esc, note: we assume the ESC is in 3D mode
    esc = new DShotRMT(ESC_PIN);
    esc->begin(DSHOT300, ENABLE_BIDIRECTION, MOTOR_POLE_COUNT);

    servo_1 = new Servo();
    servo_2 = new Servo();

    //moved to resume()
    //servo_1->attach(SERVO_1_PIN);
    //servo_2->attach(SERVO_2_PIN);




    radio = new RadioNowHandler();
    //blinker = new BlinkerHandler(LED_BUILTIN);
    mr_trig = new FastTrig();



    //for voltmeter
    pinMode(VOLTMETER_PIN, INPUT);

    //for motors
    pinMode(MOTOR_1A_PIN, OUTPUT);
    pinMode(MOTOR_1B_PIN, OUTPUT);

    pinMode(MOTOR_2A_PIN, OUTPUT);
    pinMode(MOTOR_2B_PIN, OUTPUT);

    pinMode(MOTOR_3A_PIN, OUTPUT);
    pinMode(MOTOR_3B_PIN, OUTPUT);

    pinMode(MOTOR_SLEEP_PIN, OUTPUT);

    pause();

}


RobotHandler::~RobotHandler()
{
    delete(radio);
    //delete(blinker);
    delete(mr_trig);
}


void RobotHandler::update()
{

    //pulse test
    // blinker->update();
    // if(gTimer.DeltaTimeMillis(&last_time, 1000))
    // {
    //     blinker->blink_lt(100);
    // }

    //does basic IO processing, good for testing
    //TestMain();



    if(radio->CheckForPacket(NULL) == RX_SUCCESS)
    {
        //take rx packets and format them for each application
        MapControllerData();

        //check for remote halt
        if(remote_disable)
            pause();
        else
            resume();

    }
    else if(radio->GetDeltaTime() > KEEPALIVE_TIMEOUT_MS)
    {
        //signal loss estop
        pause();
    }


    //send back information about the robot on regular intervals
    SendTelemetry();

    //do the omniwheel math
    SetWheelSpeedProportions();


    //estop enabled, don't execute any physical functions
    if(!is_enabled)
        return;

    //analogWrite to each motor driver
    WriteMotors();

    //DumpChannelPacket();

}


void RobotHandler::pause()
{
    if(!is_enabled)
        return;
    
    is_enabled = false;


    servo_1->detach();
    servo_2->detach();


    //disable wheelbase
    digitalWrite(MOTOR_SLEEP_PIN, LOW);

    //no need to disable ESC: simply not writing to it will disable it (esp32)

    Serial.println("Paused!");

    //just in case a re-enable signal comes in, (or the timer overflows), the robot will not lurch suddenly
    xm = 0;
    ym = 0;
    esc_set_speed = ESC_SPEED_MIN_R;

}


void RobotHandler::resume()
{
    if(is_enabled)
        return;

    is_enabled = true;


    servo_1->attach(SERVO_1_PIN, SERVO_1_MS_MIN, SERVO_1_MS_MAX);
    servo_2->attach(SERVO_2_PIN, SERVO_2_MS_MIN, SERVO_2_MS_MAX);


    //enable wheelbase
    digitalWrite(MOTOR_SLEEP_PIN, HIGH);

    Serial.println("Resumed!");
}


void RobotHandler::DumpChannelPacket()
{
    //dump recieved channels
    for(int i = 0; i < ANALOG_CHANNEL_CNT; ++i)
    {
        Serial.printf(" %d :%4d ||", i, radio->GetLastControlPacket().channels.analog_channels[i]);
    }
    Serial.printf("|//|");
    for(int i = 0; i < DIGITAL_CHANNEL_CNT * 2; ++i)
    {
        Serial.printf("%d :%2d ||", i, radio->GetLastControlPacket().channels.digital_channels[i]);
    }
    Serial.printf("\n");
}

void RobotHandler::DumpMappedPacket()
{
    //dump recieved channels
    //Serial.printf("XM: %5d YM: %5d ROT: %5d\n", xm, ym, rot_m);
    //Serial.printf("M1: %5d M2: %5d M3: %5d\n", mot1, mot2, mot3);

}


void RobotHandler::MapControllerData()
{
    auto gotten_data = radio->GetLastControlPacket().channels;
    
    // if(gotten_data.analog_channels[TURN_IN] > 300 || gotten_data.analog_channels[TURN_IN] < 240)
    // {
    //     Serial.println(gotten_data.analog_channels[TURN_IN]);
    // }


    xm = map(gotten_data.analog_channels[X_IN], NORMAL_MIN, NORMAL_MAX, -XY_RADIUS, XY_RADIUS);
    ym = map(gotten_data.analog_channels[Y_IN], NORMAL_MIN, NORMAL_MAX, -XY_RADIUS, XY_RADIUS);

    //do non-linear rotation mapping
    rot_m = map(gotten_data.analog_channels[TURN_IN], NORMAL_MIN, NORMAL_MAX, XY_RADIUS, -XY_RADIUS);

    float degrees = mapf(gotten_data.analog_channels[TURN_RAMP_TUNE], NORMAL_MIN, NORMAL_MAX, 1.0, 5.0);
    rot_m = (int16_t)TurnMap(rot_m, XY_RADIUS, XY_RADIUS, degrees, 0);

    //TEST
    //temp_servo2_min = map(gotten_data.analog_channels[TURN_RAMP_TUNE], NORMAL_MIN, NORMAL_MAX, SERVO_2_MS_MAX - 100, SERVO_2_MS_MAX + 100);
    //temp_servo2_max = map(gotten_data.analog_channels[MOTOR_RAMP_TUNE], NORMAL_MIN, NORMAL_MAX, SERVO_2_MS_MIN - 100, SERVO_2_MS_MIN + 100);



    //we may want to use exponential mapping for this instead to get the finer values
    ramp_tune = mapf(gotten_data.analog_channels[MOTOR_RAMP_TUNE], NORMAL_MIN, NORMAL_MAX, 0.0, 3.0);

    is_flipped_over = gotten_data.digital_channels[FLIPOVER_IN] < 1;
    is_two_wheeled = gotten_data.digital_channels[TWO_MODE_IN] > 1;
    broken_wheel = gotten_data.digital_channels[TWO_SELECT_IN];
    remote_disable = gotten_data.digital_channels[MASTER_ENABLE] == 2;

    esc_reversed = gotten_data.digital_channels[ESC_REVERSE_IN];

    //from the back right lever, controls how far the servo arm will rotoate with the stick (0-180)
    servo_angle_min = map(gotten_data.analog_channels[SERVO_MIN_IN], NORMAL_MAX, NORMAL_MIN, SERVO_MIN, SERVO_MAX);

    //reverse mapping (for servo) happens later (because both servos take different values)
    servo_angle = map(gotten_data.analog_channels[SERVO_IN], NORMAL_MAX, NORMAL_MIN, servo_angle_min, SERVO_MAX);


    //handles reverse mapping (for ESC)
    esc_set_speed = esc_reversed == 1 ? DSHOT_CMD_MOTOR_STOP : 
    (!!is_flipped_over ^ !!esc_reversed) ? 
    map(gotten_data.analog_channels[ESC_IN], NORMAL_MAX, NORMAL_MIN, ESC_SPEED_MIN_F, ESC_SPEED_MAX_F) :
    map(gotten_data.analog_channels[ESC_IN], NORMAL_MAX, NORMAL_MIN, ESC_SPEED_MIN_R, ESC_SPEED_MAX_R);


}
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

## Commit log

2024-01-24 begin framework for main program
    [configuration.h]
2024-01-24 oops: wrong folder
    swap final and test project
    [configuration.h]
2024-01-26 work on remote program code
    [configuration.h]
2024-01-31 Add rolled back firmware to debug main
    this firmware is known to transmit packets successfully
    [configuration.h]
2024-02-01 CAD updates
    [HoleSizeTest.stl]
2024-02-02 begin schematic work
    [Mainboard.kicad_pcb, Mainboard.kicad_sch]
2024-02-02 updates to CAD and schematic
    [Mainboard.kicad_sch]
2024-02-02 more schematic updates
    [Mainboard.kicad_pcb, Mainboard.kicad_sch]
2024-02-02 PCB work
    trying to cram everything on there
    [Mainboard.kicad_pcb, Mainboard.kicad_sch, Omniwheel_T1.stl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]
2024-02-05 finish omniwheel design
    begin work on main frame
    [Omniwheel_T3-1_Hub.stl, Omniwheel_T3-2_Hub.stl, Omniwheel_T3-3_Hub1.stl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]
2024-02-07 shift from STM32 to ESP32
    on the robot control surface
    [Mainboard.kicad_pcb, Mainboard.kicad_sch]
2024-02-08 update schematic and CAD
    [Mainboard.kicad_pcb]
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2024-02-10 finish first revision PCB
    [Mainboard.kicad_pcb, Mainboard.kicad_sch]
2024-02-11 rework radio class
    telemetry packets now come as part of the ACK, so there is less chance of both transmitters stepping on each other.
    [Mainboard.kicad_pcb, configuration.h]
2024-02-13 begin work on transmitter PCB
    [Transmitter.kicad_pcb, Transmitter.kicad_sch]
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2024-02-14 edit bom, work on normalizing PPM
    [MachineBOM.xlsx, configuration.h]
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2024-02-16 fix problems with PPM libarary
    it was a controller problem, but the PPM reader needs to know how to see it.
    [MachineBOM.xlsx, configuration.h]
2024-02-16 initial outlier processing removal
    still exist in-code, but is commented out
    [MachineBOM.xlsx, configuration.h]
2024-02-17 last working state before major changes
    I changed a lot. it broke the transmission again. The code here is the last state where it works.
    [configuration.h]
2024-02-17 major program updates (working)
    Transmitter is now properly normalized and working in both directions reliably.
    [configuration.h]
2024-02-19 set up radio module on ESP32
    also worked on getting the ESP32 debugger up and running
    [Mainboard.kicad_pcb, Mainboard.kicad_sch, configuration.h]
2024-02-22 Work on weight reduction
    thin the shell in order to get the total weight under 1 lb.
    [Blade.stl, BladeArmA.stl, BladeArmB.stl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]
2024-02-22 prepare to mill PCB
    also add more sub-functions to firmware
    [Mainboard.kicad_pcb, Mainboard.kicad_sch]
2024-02-22 push PCB back to other computer
    flatcam is crashing on my laptop, but works on my desktop...
    [Mainboard.kicad_pcb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]
2024-02-22 combine schematics into a single PCB layout
    [M3ShaftCoupling_inset.stl, Mainboard.kicad_pcb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]
2024-02-28 begin physical construction
    also attempt to iron out bugs using STM32's alternate SPI pins
    [ArmMount.stl, Blade.stl, BladeArm.stl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]
2024-02-28 finish PCB
    add gerbers and update schematics
    [Mainboard-B_Cu.gbr, Mainboard-NPTH.drl, Mainboard-PTH.drl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]
2024-02-29 Port CAD to Solidworks
    Required for club certification.
    Don't get me started. I hold a strong opinion on Solidworks, to say the least.
    [ArmMount.step, ArmMount.stl, Blade.step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]
2024-02-29 Work on transmitter breakout
    [Transmitter.kicad_pcb, Transmitter.kicad_sch]
2024-03-02 work out RX/TX kinks
    final radio and final baseboard now transmit properly
    [Transmitter.kicad_sch, configuration.h]
2024-03-03 Angle arm screws for assembly
    [ArmMountAngled.stl, BladeArmAngled.stl, ChassisWithScrews.stl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]
2024-03-04 move updated library to PPM test project
    [configuration.h]
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2024-03-04 revise frame and export STLs
    [ArmMount.stl, BladeArm.stl, Chassis.stl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]
2024-03-07 add no-transmit on no-ppm condition
    still having other numerous software bugs
    [RoofShuntLong.stl, RoofShuntShort.stl, configuration.h]
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2024-03-09 try to iron out bugs in the program code
    some of these bugs were hardware bugs...
    [configuration.h]
2024-03-09 begin work on ESP-Now protocol
    this may be more reliable than the RFM69s
    [configuration.h]
2024-03-12 finish value transmission with ESPNow
    reliable data transfer using ESPNow is now possible
    [configuration.h]
2024-03-12 set up robot handling code
    discovered stability problems with the PPM portion of the radio code, will look into that next
    [configuration.h]
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2024-03-12 fixed PPM conflict
    add halt states to PPM library and full packet detection so that we only try to send packets that we know are complete. This slows down transmission time slightly, but it shouldn't be too much of a problem.
    [Controller.cpp, Transmitter.cpp]
2024-03-13 Fix Conflicting pin bugs and move documentation
    [configuration.h]
2024-03-16 use RMT for PPM detection
    this is hardware based, so we get a much more stable input
    [AlgorithmPlotter.xlsx, configuration.h]
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2024-03-20 Work on servo arm
    [ArmMountAngledKey.stl, ArmMountAngledKey13.5.stl, ArmMountAngledKeyShort.stl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]
2024-03-20 add the rest of the solidworks files
    Also do some minor firmware tweaks to make sure the robot works properly
    [OMNI-A-0000TLA.SLDASM, OMNI-A-0200Lid.SLDASM, OMNI-A-0300Wheel.SLDASM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]
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2024-03-23 fix pin assignments
    I did some re-soldering
    [configuration.h]
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2024-03-26 add concept for next bot
    come on, I just finished building the first one! Already I have another on the table?
    [ArmMountAngledKey13.5.stl, BladeArmShortAngledKey.stl, StationaryArmAlt.stl]
2024-06-07 Organize files and add camera jig
    [AlgorithmPlotter.xlsx, ArmMount.step, ArmMount.stl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]
2024-06-17 add an updated STL
    [TransmitterHolder.stl]
2025-01-15 experiment with blender
    and the sketcher addon
    [AuntFanny.blend]
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2025-01-22 more ideas for RB3
    [AuntFanny.blend]
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2025-02-05 work on CAD and club BOM
    [Full Combat BoM Template.xlsx]
2025-02-21 Firmware split + last commit before RB3 bevel
    [Full Combat BoM Template.xlsx, HoleSizeTest1.stl, Schematic.kicad_pcb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]
2025-03-11 lots of CAD and firmware work
    back to basics: re-establish communication between two ESP32s because that was broken in the higher-level code.
    [INFILL_ScrollLayer.stl, INFILL_ScrollLayer2.stl, MainChassis.stl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]
2025-03-12 discover problem with esp-now
    the new IDF I'm using apparently doesn't support encrypted targets...
    [configuration.h]
2025-03-12 fix esp-radio class for all firmware types
    todo: fix base transmitter code: the PPM is broken
    [configuration.h]
2025-03-19 CAD work (export for printing)
    [BearingHolder2.stl, ElectronicsCap.stl, Fan.blend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]
2025-03-22 firmware and testing
    something's broken. I don't know what...
    [Buns1.stl, Buns2.stl, Fan.stl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]
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2025-10-23 Lots of work on Robot 4
    Everything, really...
    [Fan.blend, Fan_V2.obj, Fan_V2.stl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]
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2025-11-11 More robot CAD work
    [configuration.h]
2025-11-14 Lots of work on RB4
    so much to do in so little time
    [BoltSpacer.stl, Hat.stl, LOLIN32 pinLabels_RFM.kicad_sch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]
2025-11-14 more STLs and firmware testing
    [BackCap.stl, BigWheel.stl, BigWheelMold.stl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]
2025-11-17 Finish the thing before competition day
    This robot is cursed
    [LOLIN32 pinLabels_RFM.kicad_sch, Schematic.kicad_sch, configuration.h]
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
